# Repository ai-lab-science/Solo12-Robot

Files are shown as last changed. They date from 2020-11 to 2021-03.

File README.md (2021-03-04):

<!--
*** Thanks for checking out this README Template. If you have a suggestion that would
*** make this better, please fork the repo and create a pull request or simply open
*** an issue with the tag "enhancement".
*** Thanks again! Now go create something AMAZING! :D
***
***
***
*** To avoid retyping too much info. Do a search and replace for the following:
***  PRGeeesus, Solo12-Robot, twitter_handle, email
-->

<!-- PROJECT SHIELDS -->
<!--
*** I'm using markdown "reference style" links for readability.
*** Reference links are enclosed in brackets [ ] instead of parentheses ( ).
*** See the bottom of this document for the declaration of the reference variables
*** for contributors-url, forks-url, etc. This is an optional, concise syntax you may use.
*** https://www.markdownguide.org/basic-syntax/#reference-style-links
-->
<!--
[![Contributors][contributors-shield]][contributors-url]
[![Forks][forks-shield]][forks-url]
[![Stargazers][stars-shield]][stars-url]
[![Issues][issues-shield]][issues-url]
[![MIT License][license-shield]][license-url]
[![LinkedIn][linkedin-shield]][linkedin-url]

-->

<!-- PROJECT LOGO -->
<br />
<p align="center">
  
  <h3 align="center">Solo12-Robot</h3>

  <p align="center">
    This repo summarizes my changes to the Open Dynamics Robot Initiative Project.
    <br />
    <a href="https://github.com/ai-lab-science/Solo12-Robot"><strong>Explore the docs »</strong></a>
    <br />
    <br />
    <a href="https://github.com/ai-lab-science/Solo12-Robot">View Demo</a>
    ·
    <a href="https://github.com/ai-lab-science/Solo12-Robot/issues">Report Bug</a>
    ·
    <a href="https://github.com/ai-lab-science/Solo12-Robot">Request Feature</a>
  </p>
</p>

<!-- TABLE OF CONTENTS -->
## Table of Contents

* [About the Project](#about-the-project)
  * [Useful Links](#Useful-Links)
* [Changes Made to Original](#All-changes-Made-to-Original)
  * [Magnetic Encoder](#Magnetic-Encoder)
  * [M3 Belts and Pulleys](#M3-Belts-and-Pulleys)
  * [Motor and Center Pulley](#Motor-and-Center-Pulley)
  * [20x20 Hip AA Bearings](#20x20-Hip-AA-Bearings)
  * [Foot Contact Switch](#Foot-Contact-Switch)

* [Supplier Links](#Supplier-Links)
* [License](#license)
* [Contact](#contact)
* [Acknowledgements](#acknowledgements)

<!-- ABOUT THE PROJECT -->
## About The Project
TODO
TODO

#### Useful Links

* [Original Project by the Open Dynamic Robot Initiative](https://github.com/open-dynamic-robot-initiative/open_robot_actuator_hardware)

* [To-Dos for this Project](https://github.com/ai-lab-science/Solo12-Robot/issues)

---
<!-- All changes Made to Original -->
## All changes made to the original

Here you can find the Documentation of all changes that were made to the original Robot.

---
### Magnetic Encoder

The original Robot uses an optical Encoder. Due to its cost and the effort in assembly this was replaced with a magbetic enoder by AMS called [AS5047](https://ams.com/AS5047P).

| Encoder Changes Mechanical | Encoder Changes Electrical | Config. and Arduino | uDriver |
|---|---|---|---|
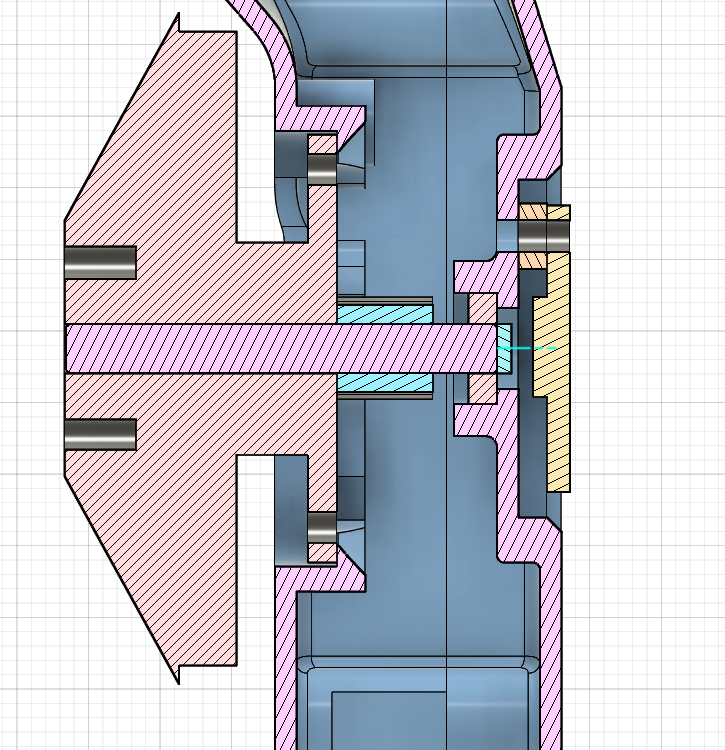
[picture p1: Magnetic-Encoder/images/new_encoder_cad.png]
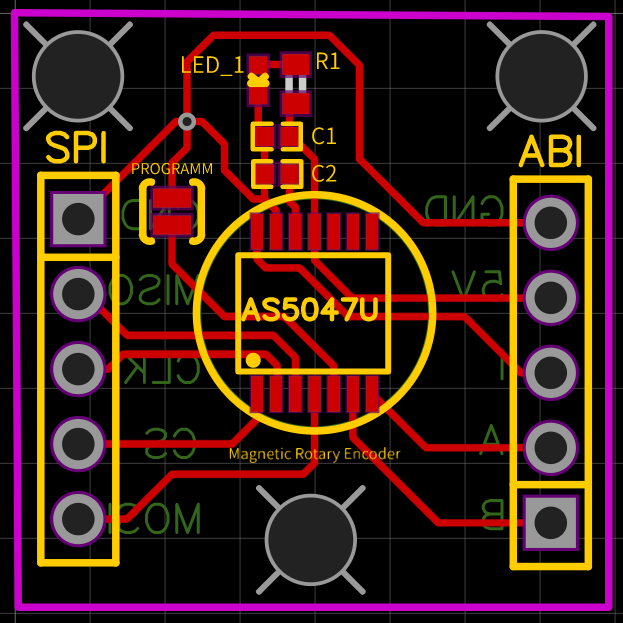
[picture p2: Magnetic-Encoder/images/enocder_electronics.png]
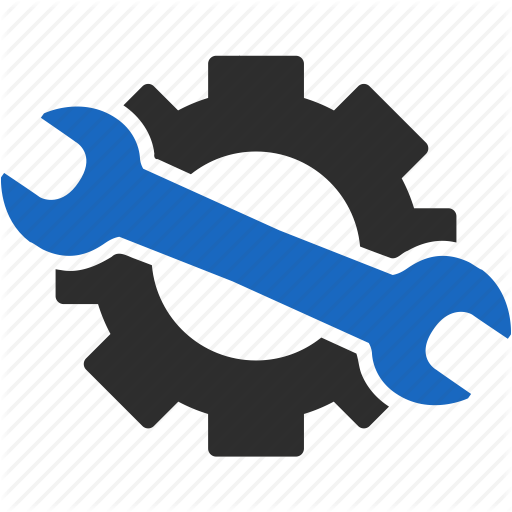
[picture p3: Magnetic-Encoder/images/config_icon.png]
| |  | ||

<!-- M3 Belts and Pulleys -->
---
### M3 Belts and Pulleys
The original Pulleys and Belts were repalced with M3 Pulleys and the fitting Belts.

* The new Belts were bought [here](https://www.zahnriemen24.de/a/40007-zahnriemen-3m)
* The new Pulleys were bought [here](https://www.zahnriemen24.de/a/40139-zahnscheiben-3m?vorbohrungspannsatz=1&bohrung=1&zaehnezahl=10&quantity=1)

The .STL files of the Pulleys were also updated:
|center pulley|Output Pulley|
|---|---|
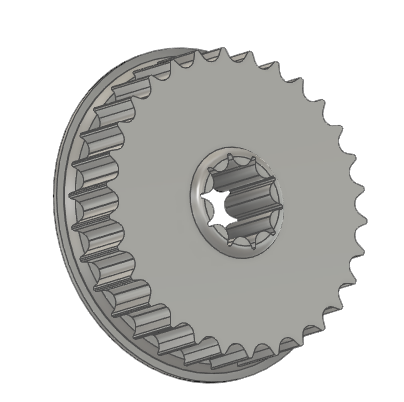
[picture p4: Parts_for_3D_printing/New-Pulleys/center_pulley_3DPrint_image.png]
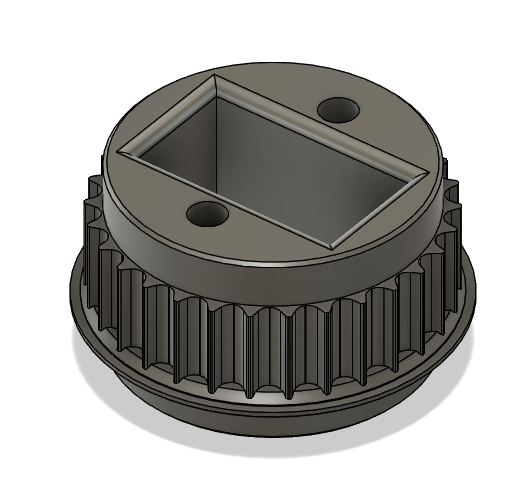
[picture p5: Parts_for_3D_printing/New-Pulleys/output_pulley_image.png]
|||
|[.stl New Center Pulley](Parts_for_3D_printing/New-Pulleys/pulley_center_30t.stl)|[.stl New Output Pulley](Parts_for_3D_printing/New-Pulleys/pulley_output_30t.stl)|

---
### Motor and Center Pulley
The Motor Pulley, Center Pulley and Motor Shaft were machined according to:
| |Motor Pulley|Center Pulley|Motor Shaft|
|---|---|---|---|
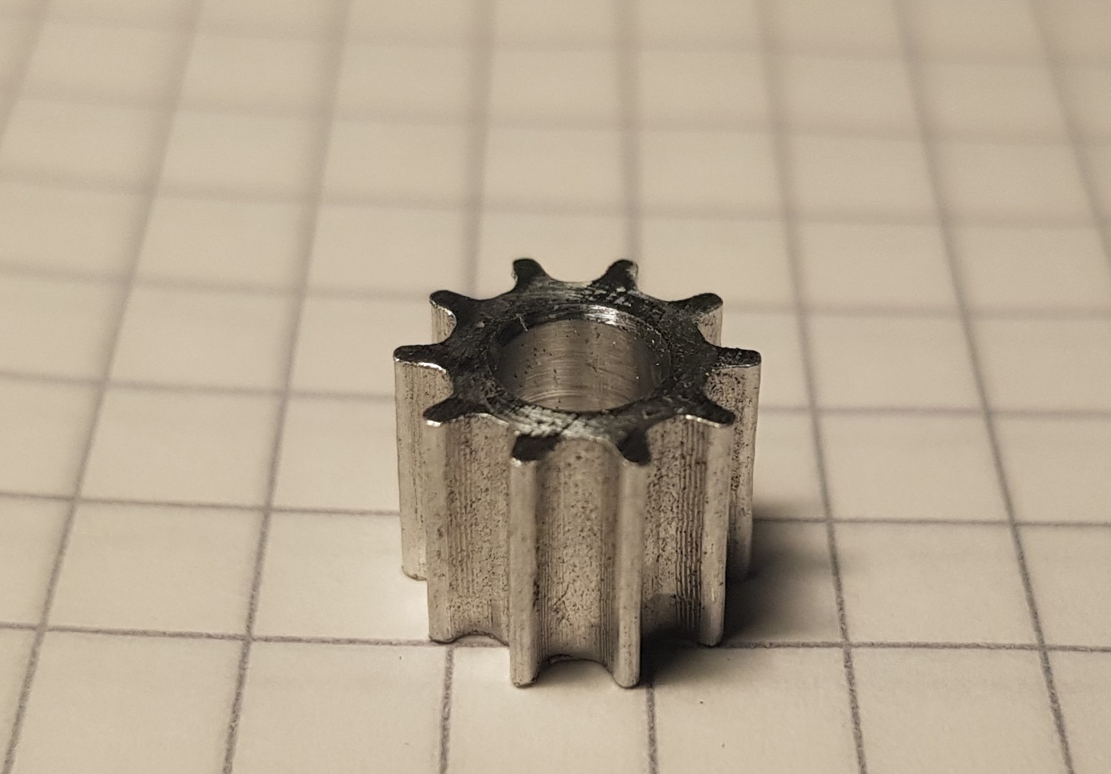
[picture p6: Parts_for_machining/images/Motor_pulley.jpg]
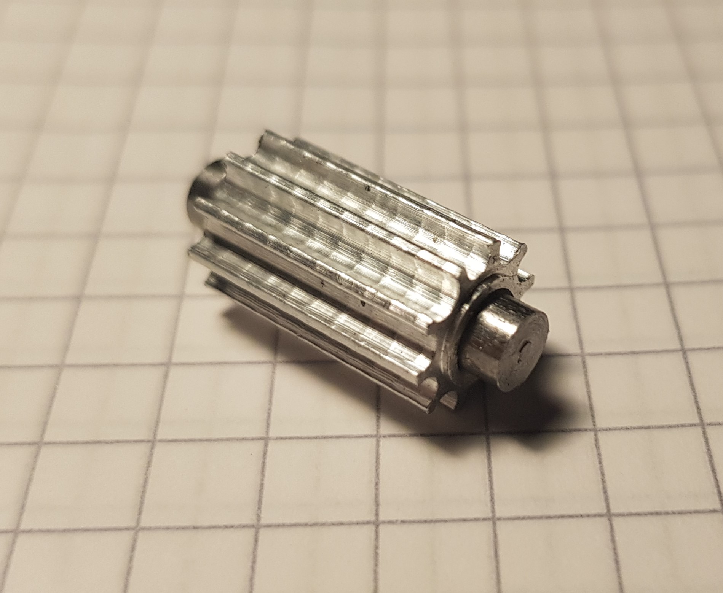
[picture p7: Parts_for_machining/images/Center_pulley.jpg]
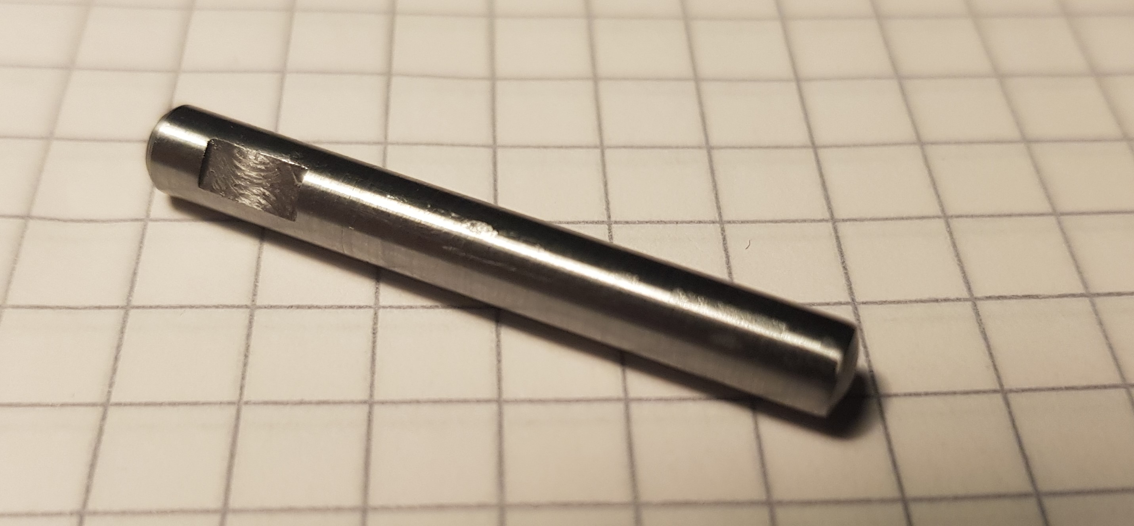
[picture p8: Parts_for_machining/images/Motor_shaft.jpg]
|Manufactured:||||
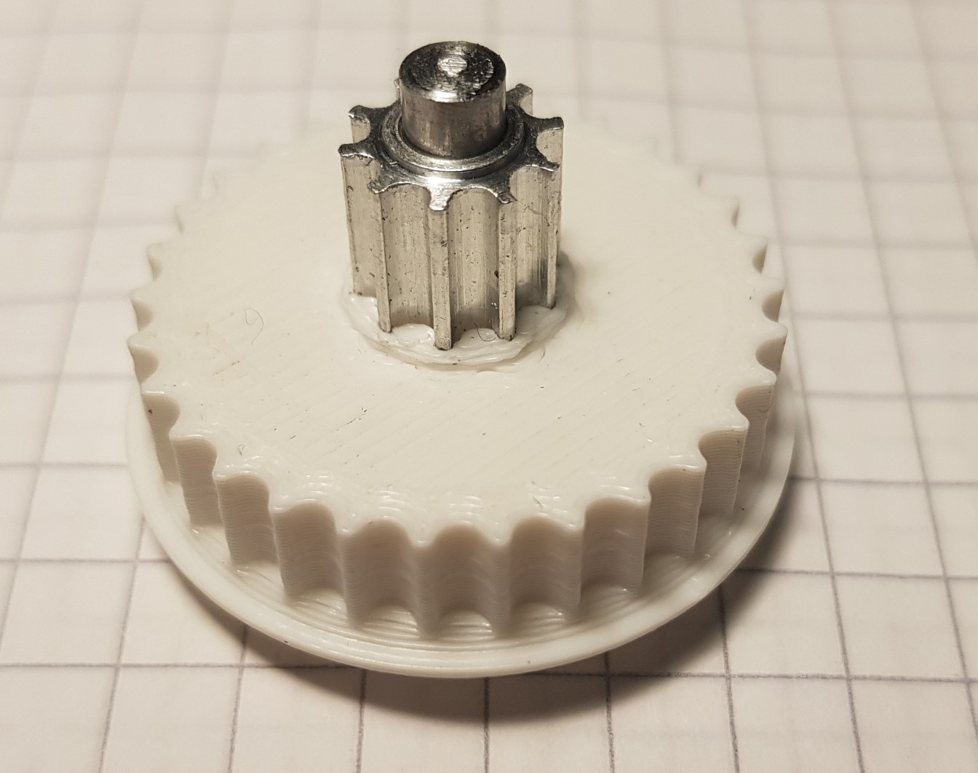
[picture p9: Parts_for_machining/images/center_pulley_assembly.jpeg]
|Assembly||||
|Machining Instructions PDF:|<a href="\Parts_for_machining\new_motor_Pulley_Zeichnung_v2.pdf" target="_blank">Motor Pulley</a>|<a href="\Parts_for_machining\New_Center_Pulley_10_teeth_Zeichnung_v0.pdf" target="_blank">Center Pulley</a>|<a href="\Parts_for_machining\motor_antigravity_4004_custom_shaft_Zeichnung_v1.pdf" target="_blank">Motor shaft</a>

* Parts in a lathe until they matched the Drawings:

<br>
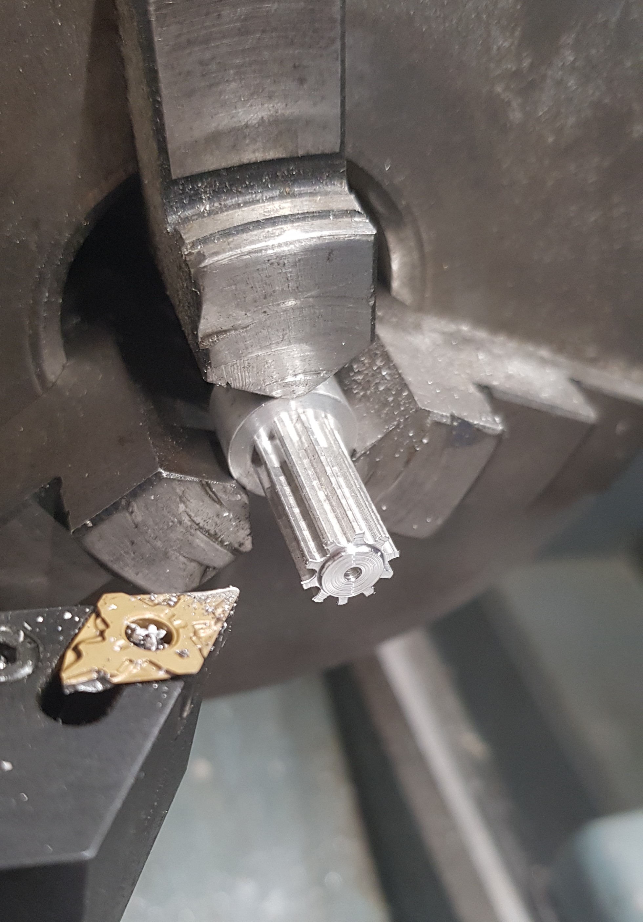
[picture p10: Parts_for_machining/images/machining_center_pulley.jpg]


---
### 20x20 Hip AA Bearings
 The "Hip AA Bearing" of size 25 x 20 x 4mm were replaced with bearings of 27 x 20 x 4mm because of availability. The [.stl](\Parts_for_3D_printing\hip_aa_fromt_cover_27.2mm_bearing.stl) files were updated accordingly. The bearings were bought [here](https://www.123kugellager.de/lager-R2520-2Z-ZEN).

---
### Foot Contact Switch

* no foot contact switch was added yet. However, the cables are fed through for future add-on.
[Link](Foot-Contact-Switch/README.md)

## Supplier Links
All other parts were bought as described. I divided the Project into 3 parts.
Here is a table for all parts from the Main Body:

| Part | Description | Suppliers |
|---|---|---|
| Hip AA Bearing | Bearing to attach Hip FE to the body | [123kugellager.de](https://store-en.tmotor.com/goods.php?id=438)|
| Fasteners | All fasteners as described by the original  | [online-schrauben.de](https://online-schrauben.de/shop/) |
<br>
Here is a table for all parts for one 3 DoF Leg:<br><br>

| Part | Description | Suppliers |
|---|---|---|
| T-Motor Antigravity 4004 300kV | Motor for the actuator | [T-Motor Store](https://www.123kugellager.de/lager-R2520-2Z-ZEN)|
| Fasteners | All fasteners as described by the original  | [online-schrauben.de](https://online-schrauben.de/shop/) |
| Timing Belt 4mm / length: 150mm / 50 teeth | new M3 Timing Belts  | [www.zahnriemen24.de](https://www.zahnriemen24.de/a/40007-zahnriemen-3m) |
| Timing Belt 6mm / length: 201mm / 67 teeth | new M3 Timing Belts  | [www.zahnriemen24.de](https://www.zahnriemen24.de/a/40007-zahnriemen-3m) |
|Bearing Output Shaft 32mm x 25mm x 4mm | bearing for each output | [ekugellager.de](https://www.ekugellager.de)|
|Bearing Motor Shaft and Center Shaft |8mm x 4mm x 2mm bearing | " |[ekugellager.de](https://www.ekugellager.de)|
|Bearing Timing Belt Tensioner| - | " |
|Motor Shaft| new shaft | [reidl.de](https://www.reidl.de/iso-8740-zylinderkerbstifte-mit-fase?q=stahlzylinder)
|Motor and Center Pulley| new M3 Pulleys| [www.zahnriemen24.de](https://www.zahnriemen24.de/a/40139-zahnscheiben-3m?vorbohrungspannsatz=1&bohrung=1&zaehnezahl=10&quantity=1)|

## License

Distributed under the MIT License. See `LICENSE` for more information.

<!-- CONTACT -->
## Contact

martin.buchschuster@student.uni-luebeck.de

Project Link: [This-site](https://github.com/ai-lab-science/Solo12-Robot)

<!-- ACKNOWLEDGEMENTS -->
## Acknowledgements

* [Ralf Bruder]()
* [Elmar Rueckert]()
* [Martin Buchschuster]()

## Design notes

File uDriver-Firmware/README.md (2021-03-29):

### Motorware modifications

The firmware of the uDrivers has to be modified:

* In the file "user_j1.h", "user_j5.h", "user_mtr_on_j1.h", "user_mtr_on_j5.h" #define USER_MOTOR_ENCODER_LINES changed to ().

| in file | output in SPI |
|---|---|
|133.7|852143|
|1024.0|65735|
|32768.0|28|
|65536.0|7|
|131072.0|3|
|262144.0|1|

---

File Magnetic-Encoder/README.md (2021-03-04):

## Encoder Adaptation

The Optical encoder, enocder wheel and mount were replaces woth a magentic encoder.
For this, the AS5047 is mounted facing the end of the of shaft, to which a magnet is attached.
The Covers were modified to accept the footprint of the PCB.
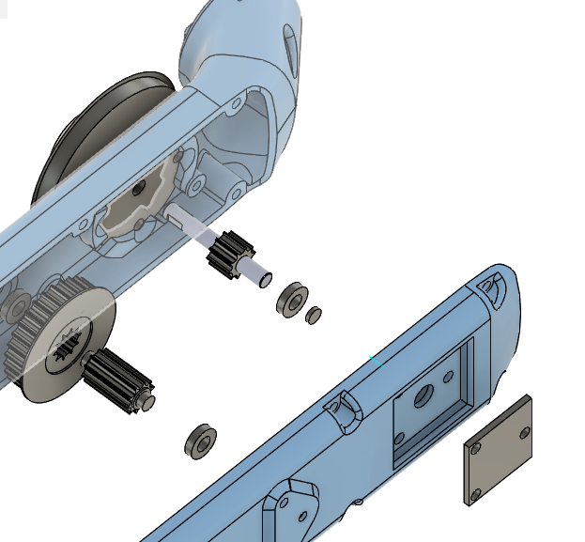
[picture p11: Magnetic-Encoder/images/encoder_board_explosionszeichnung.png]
<br><br>

## Mechanical Changes

All the covers of the leg modules were equipped with a recess of 3mm debth to hold the encoder board. The Motor-shaft was shortened by 3mm aswell. At the end of the shaft now sits a magnet that gives the rotational inofrmation to the AS5074.
Three holes for mounting as well as spacers are also given.

---
### Magnet for the Encoder
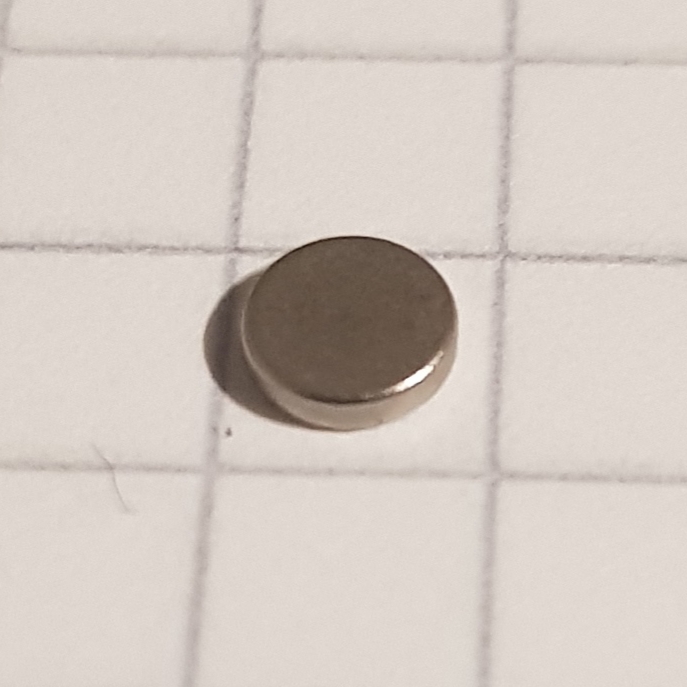
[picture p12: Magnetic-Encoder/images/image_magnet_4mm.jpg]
<br>
* [Magnets Retailer](https://www.magnetkontor.de/products/de/Neodym-Magnete-Rohmagnete/Auswahl-besond-Eigenschaft/diametral-magnetisiert/NdFeB-N52-Scheibenmagnet-4-x-1-mm-vernick-diametr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)<br>

---
### New Shell Covers

* The list of STL files for 3d printing the new shells can be found here: [STL files 3dof leg](stl_files). TODO: Link to new .stl Files

|Hip AA| Hip FE| Upper Leg|
|---|---|---|
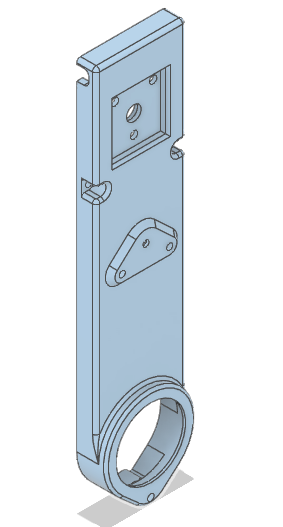
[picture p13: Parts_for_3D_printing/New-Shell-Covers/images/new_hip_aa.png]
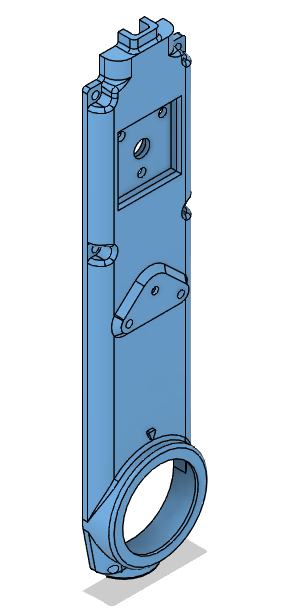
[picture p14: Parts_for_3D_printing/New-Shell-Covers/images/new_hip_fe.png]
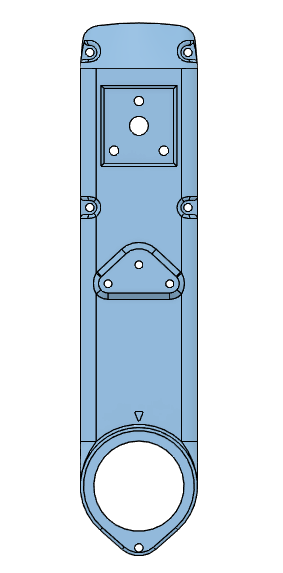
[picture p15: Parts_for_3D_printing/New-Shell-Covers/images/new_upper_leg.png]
|||
|[Hip AA Module New Shell Cover - STL file](../Parts_for_3D_printing/New-Shell-Covers/cover_hip_aa.STL)|[Hip FE Module New Shell Cover - STL file](../Parts_for_3D_printing/New-Shell-Covers/cover_hip_fe.STL)|[Upper Leg Module New Shell Cover - STL file](../Parts_for_3D_printing/New-Shell-Covers/cover_upper_leg.STL)

---
## Electrical changes

As the micro Drivers Require ABI input for the tourque control, the encoders can output ABI, as well as SPI in order tp have the position input ready for the [Master-Board](https://github.com/open-dynamic-robot-initiative/master-board#master-board).

---
### Gerber Files

|PCB Schematic|Photograph|
|---|---|
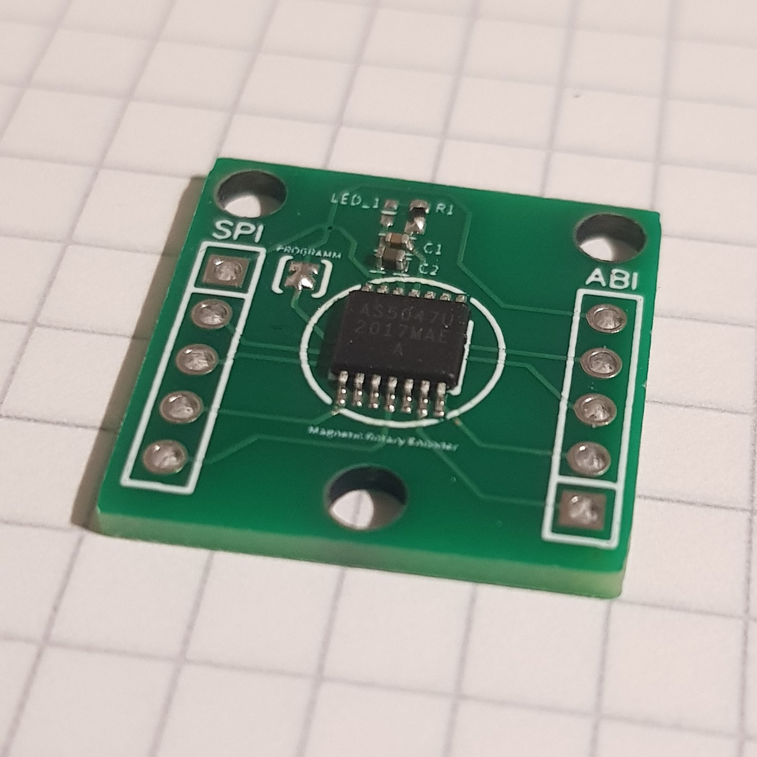
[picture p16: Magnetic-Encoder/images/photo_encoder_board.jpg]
|  | |

* The gerber files for the encoder Bord can be found [Here](/Electrical-Changes)

---
### Bill of Material

| Part | Description | Suppliers |
|---|---|---|
| AS5047 | main IC | [Mouser](mouser.com)|
| C1 | Cap. 0402 100 nf  | " |
| C2 | Cap. 0402 1 uf  | " |
| R1 | optional. 100R for LED_1  | " |
| LED_1 | 0402 LED  | " |

---
### Wires

* The magnetic encoders are wired with as two flatband cables. The colors are the same on all encoders.

|Flatband Cables|Description
|---|---|
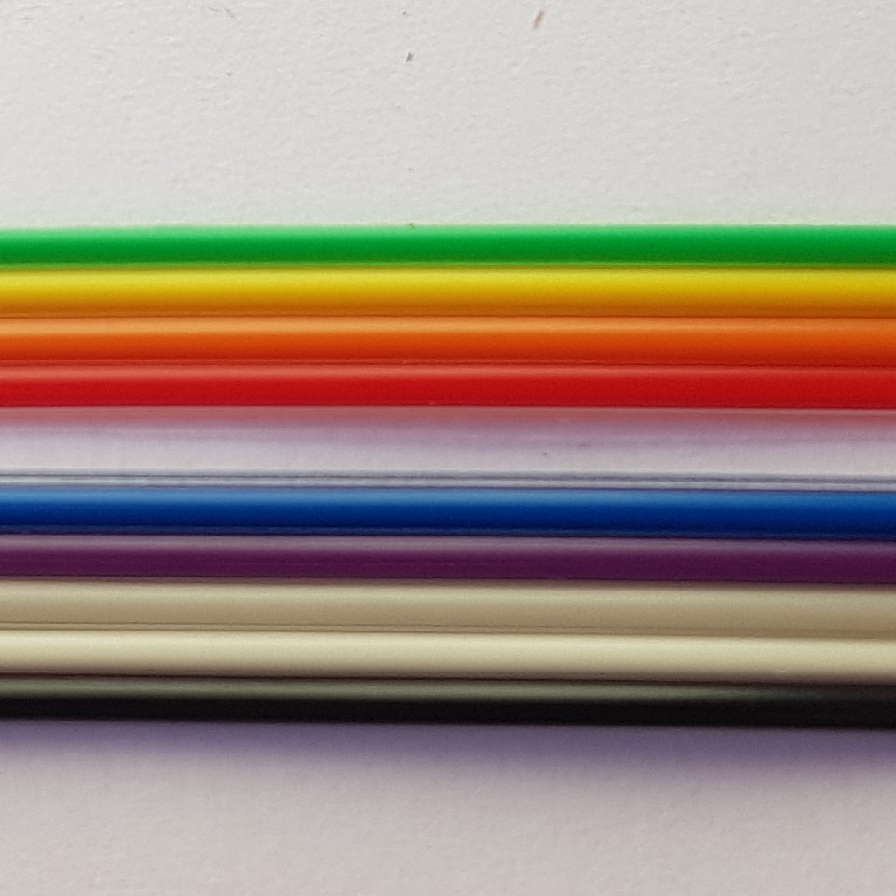
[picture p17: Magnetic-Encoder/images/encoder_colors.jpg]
|  |<table><thead><tr><th>Color</th><th>Pin</th> <th>Description</th></tr></thead><tbody><tr><td>Green</td><td>MOSI</td><td>Master Out Slave In (SPI)</td></tr><tr><td>Yellow</td><td>CS</td><td>chip Select (SPI)</td></tr><tr><td>Orange</td><td>CLK</td><td>clock (SPI)</td></tr><tr><td>Red</td><td>MISO</td><td>Master in Slave Out (SPI)</td></tr>
<tr><td>Marine Blue</td><td>B</td><td>for ABI</td></tr><tr><td>Purple</td><td>A</td><td>"</td></tr><tr><td>Grey</td><td>I</td><td>"</td></tr><tr><td>White</td><td>5V</td><td>Power supply</td></tr><tr><td>Black</td><td>GND</td><td>Ground for SPI and ABI</td></tr></tbody></table>|

<br>

---
## Communication Via Arduino

The AS5047 is should be connected via SPI [Wires](#Wires) to any other Arduino with SPI.
Then following Code can be used to program the AS5047 tempoararily. The solder bridge "Test" should be closed for this.
* [Code: Program AS5047U_OTP](Arduino)

By removing the while(1) the programming will be OTP.

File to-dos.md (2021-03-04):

# TODOS for this Project:

|Name|Descriptions|
|----|----|
|Foot contact Sensor|Add a foot contact sensor to all legs. The cables are already existing. The ODRI also had a Sensor designed already|
|Order Extra Cables|Some cabls to connect all the sencors to the uDrivers Are still missing. <br>[Details Electronic Components and Tools](https://github.com/open-dynamic-robot-initiative/open_robot_actuator_hardware/blob/master/electronics/details/details_components.md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)

<!--Test->

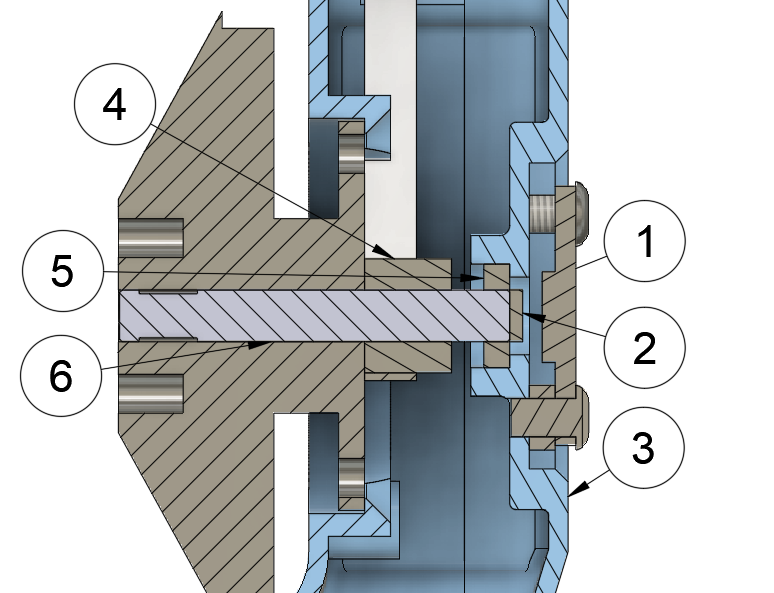
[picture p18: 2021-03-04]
Magnetic-Encoder/images/overview_2.png

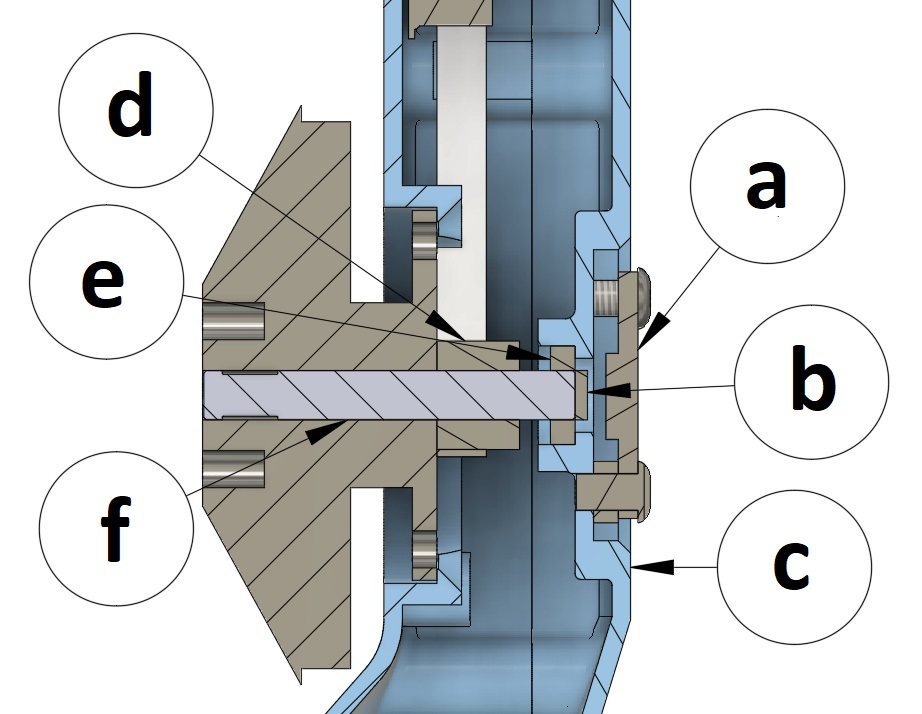
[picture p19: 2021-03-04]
Magnetic-Encoder/images/overview_1_letters.jpg

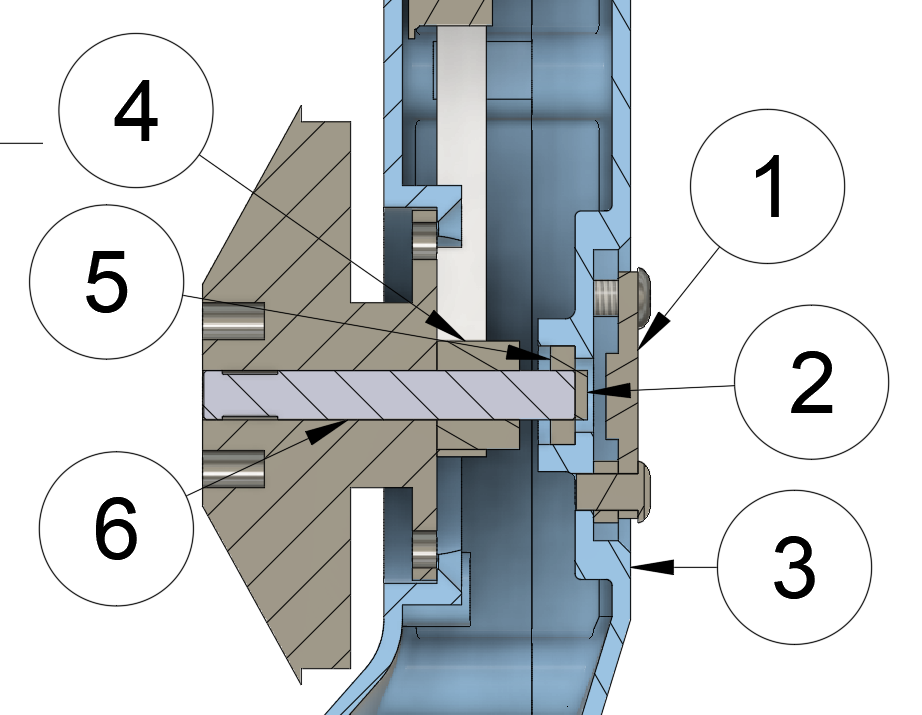
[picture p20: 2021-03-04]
Magnetic-Encoder/images/overview_1.png

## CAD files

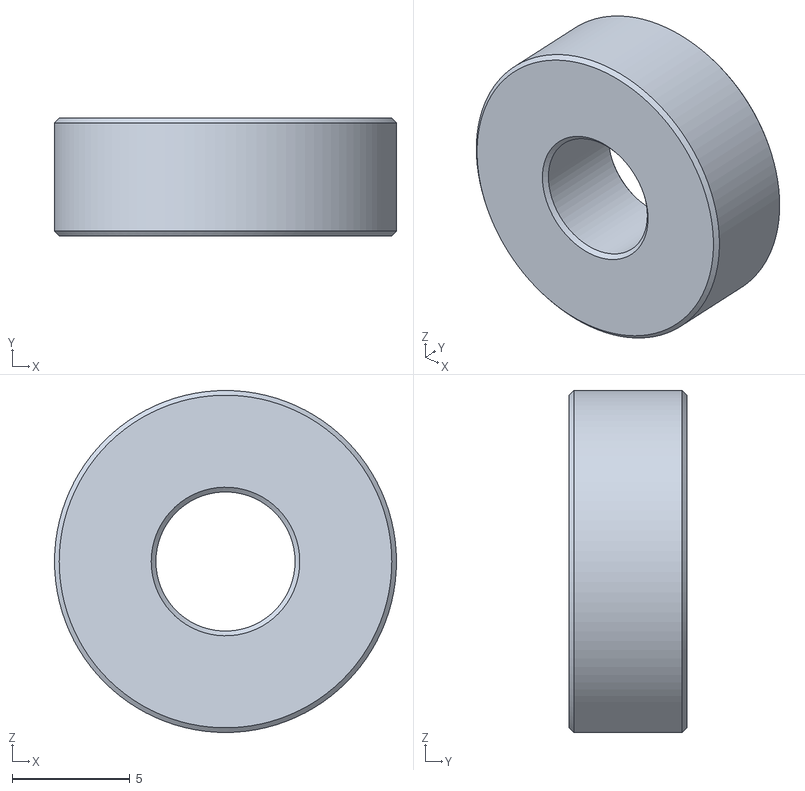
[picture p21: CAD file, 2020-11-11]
Parts_for_3D_printing/Werkzeuge/tool_center_pulley_assembly.stl
14.5 x 5.00 x 14.5

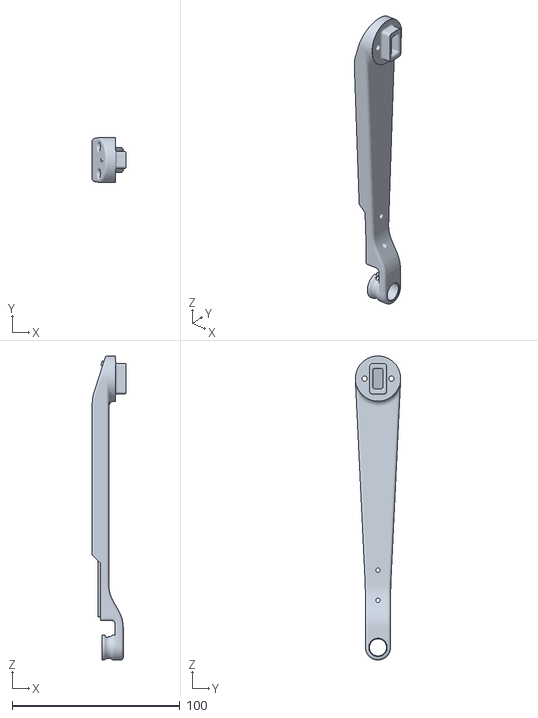
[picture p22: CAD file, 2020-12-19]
Parts_for_3D_printing/Foot/main Body.stl
20.0 x 27.0 x 181.0

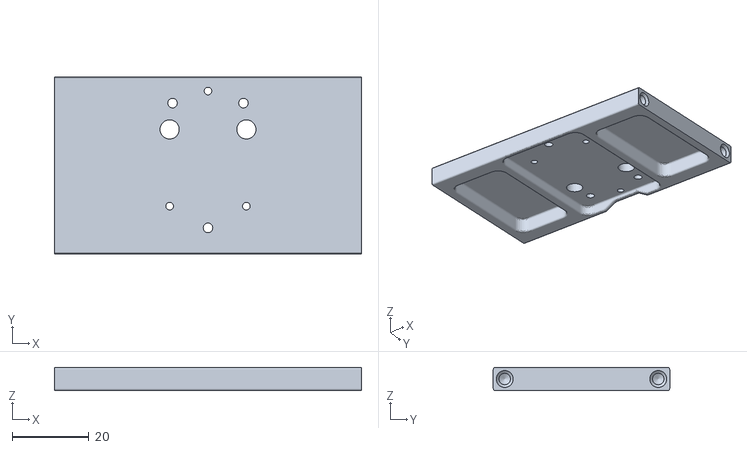
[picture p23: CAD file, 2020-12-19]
Parts_for_3D_printing/Body_new_IMU.stl
80.0 x 46.0 x 6.00

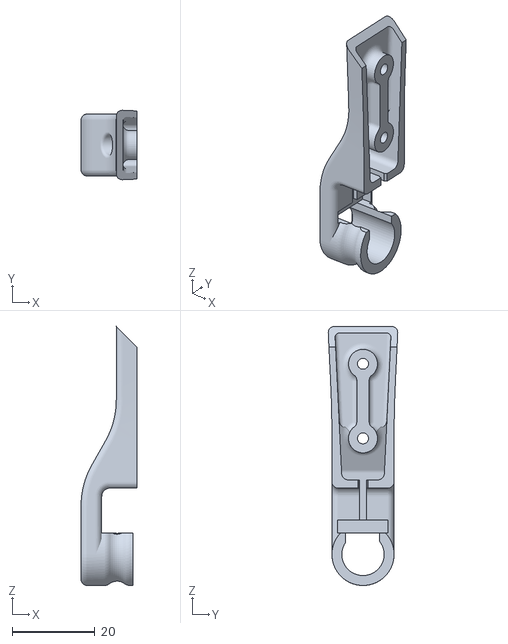
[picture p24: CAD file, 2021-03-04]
Parts_for_3D_printing/Foot/ankle_new_2.stl
13.5 x 16.8 x 62.5

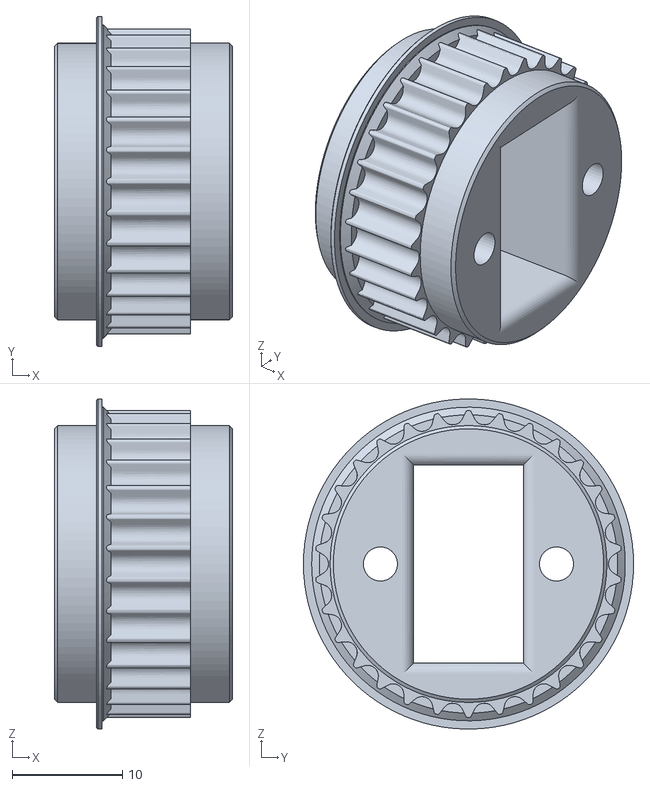
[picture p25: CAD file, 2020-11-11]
Parts_for_3D_printing/New-Pulleys/pulley_output_30t.stl
16.2 x 30.0 x 30.0

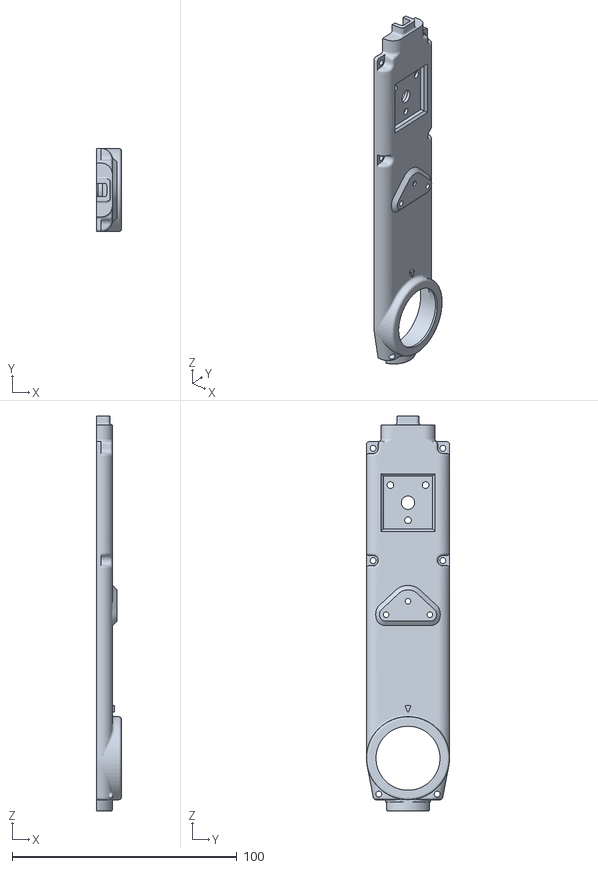
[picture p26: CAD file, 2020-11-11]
Parts_for_3D_printing/New-Shell-Covers/cover_hip_fe.stl
11.0 x 37.0 x 175.9

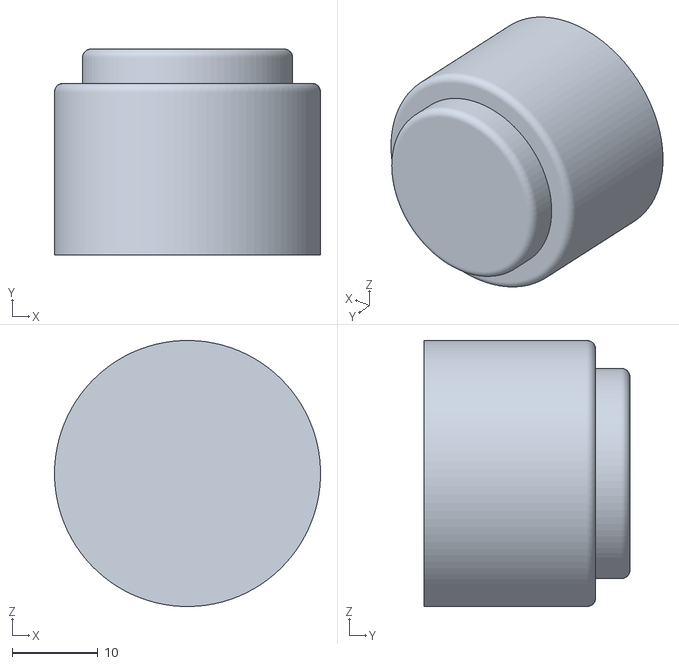
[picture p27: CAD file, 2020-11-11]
Parts_for_3D_printing/Werkzeuge/uotput_bearing_die.stl
31.0 x 24.0 x 31.0

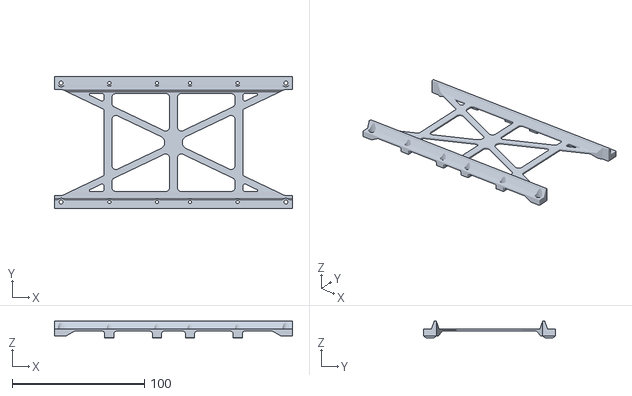
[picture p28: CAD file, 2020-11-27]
Parts_for_3D_printing/body_structure_center.STL
180.0 x 100.0 x 12.5

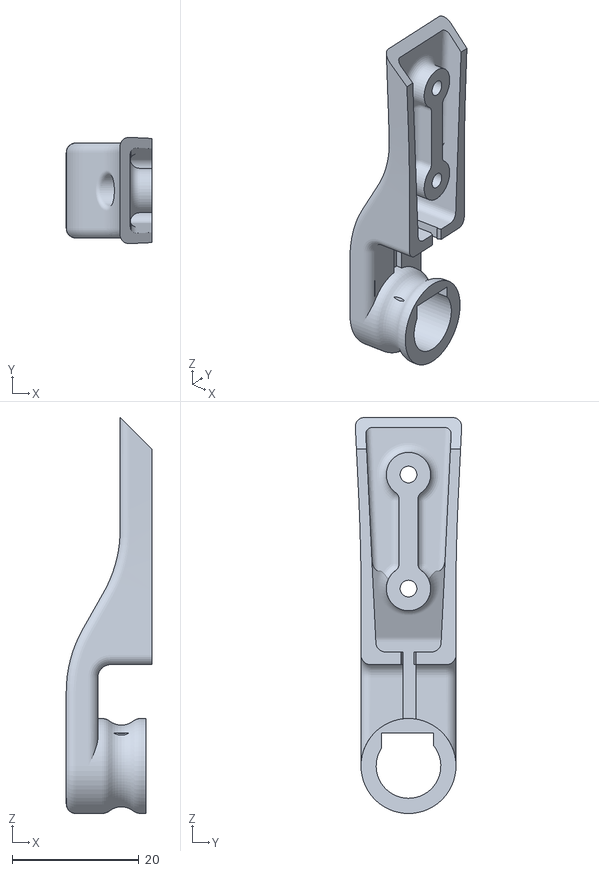
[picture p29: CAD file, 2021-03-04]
Parts_for_3D_printing/Foot/ankle_new_3.stl
13.5 x 16.8 x 62.5

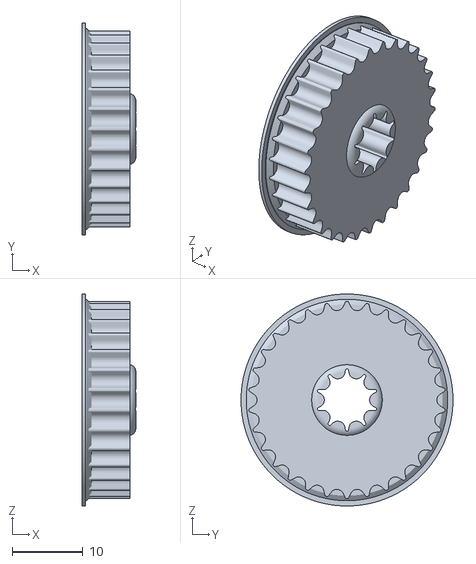
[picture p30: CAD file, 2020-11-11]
Parts_for_3D_printing/New-Pulleys/pulley_center_30t.stl
7.60 x 30.0 x 30.0

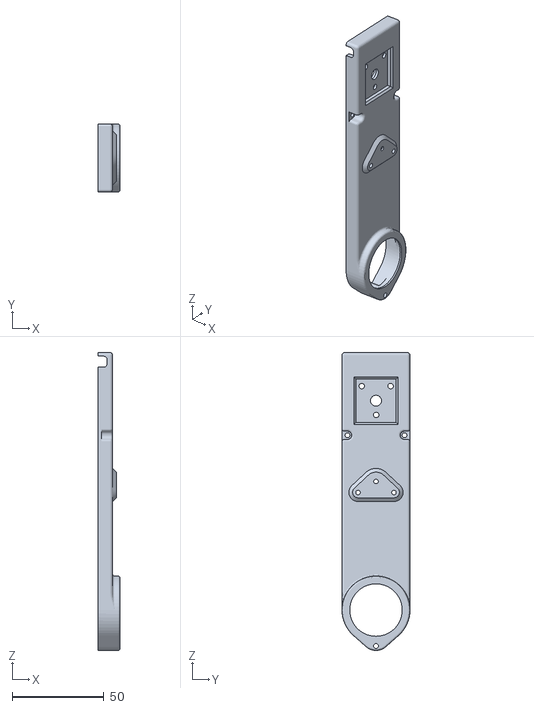
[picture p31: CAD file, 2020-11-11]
Parts_for_3D_printing/New-Shell-Covers/cover_hip_aa.stl
12.0 x 37.0 x 162.0

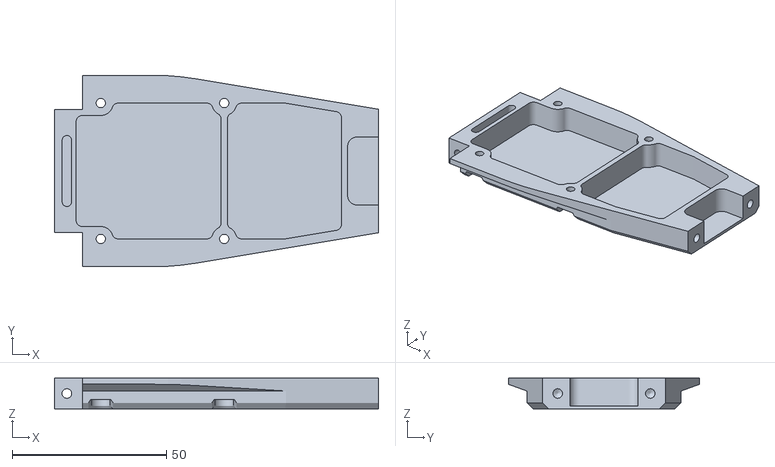
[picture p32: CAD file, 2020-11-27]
Parts_for_3D_printing/body_structure_side.STL
105.0 x 62.0 x 10.0

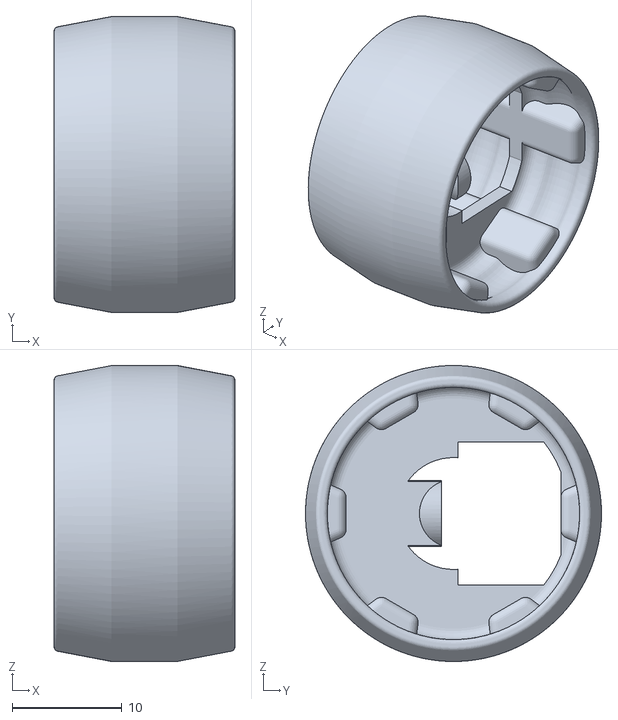
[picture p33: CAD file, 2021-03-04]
Parts_for_3D_printing/Foot/foot_palm_new_2.stl
16.5 x 27.0 x 27.0

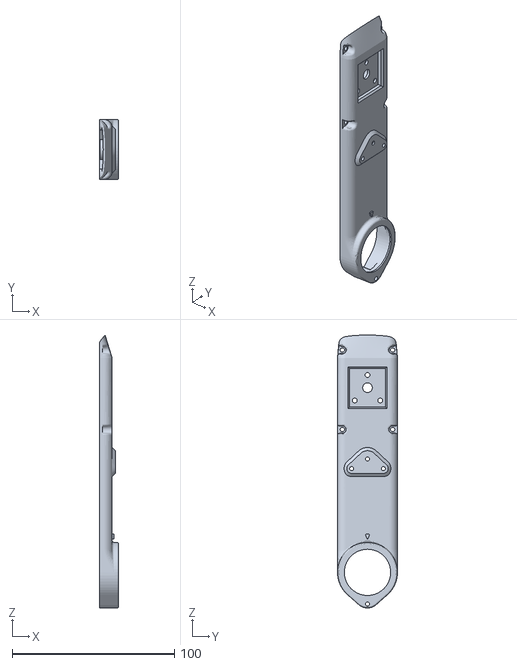
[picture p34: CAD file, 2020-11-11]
Parts_for_3D_printing/New-Shell-Covers/cover_upper_leg.stl
12.0 x 37.0 x 168.3

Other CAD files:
Parts_for_3D_printing/Werkzeuge/motor_shaft_extractor.stl
Parts_for_3D_printing/body_structure_center_handle.STL
Parts_for_3D_printing/Foot/foot_new_3.stl
Parts_for_3D_printing/Werkzeuge/center_pulley_protection v2.stl
Parts_for_3D_printing/AI3M_print2_file.3mf
Parts_for_3D_printing/Foot/Ankle.stl
Parts_for_3D_printing/Foot/Bootom of Foot.stl
Parts_for_3D_printing/Foot/Foot_new_2.stl
Parts_for_3D_printing/Foot/fake_platine.stl
Parts_for_3D_printing/Foot/foot_palm_new_3.stl
Parts_for_3D_printing/Martin_print2_side-fesupport_fecover.3mf
Parts_for_3D_printing/Martin_print3_3coveraa-1coverfe-1baseupperleg.3mf
Parts_for_3D_printing/Print_4.3mf
Parts_for_3D_printing/base_hip_aa.stl
Parts_for_3D_printing/base_hip_fe.stl
Parts_for_3D_printing/base_upper_leg.stl
Parts_for_3D_printing/body_structure_back.STL
Parts_for_3D_printing/body_structure_bottom.STL
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

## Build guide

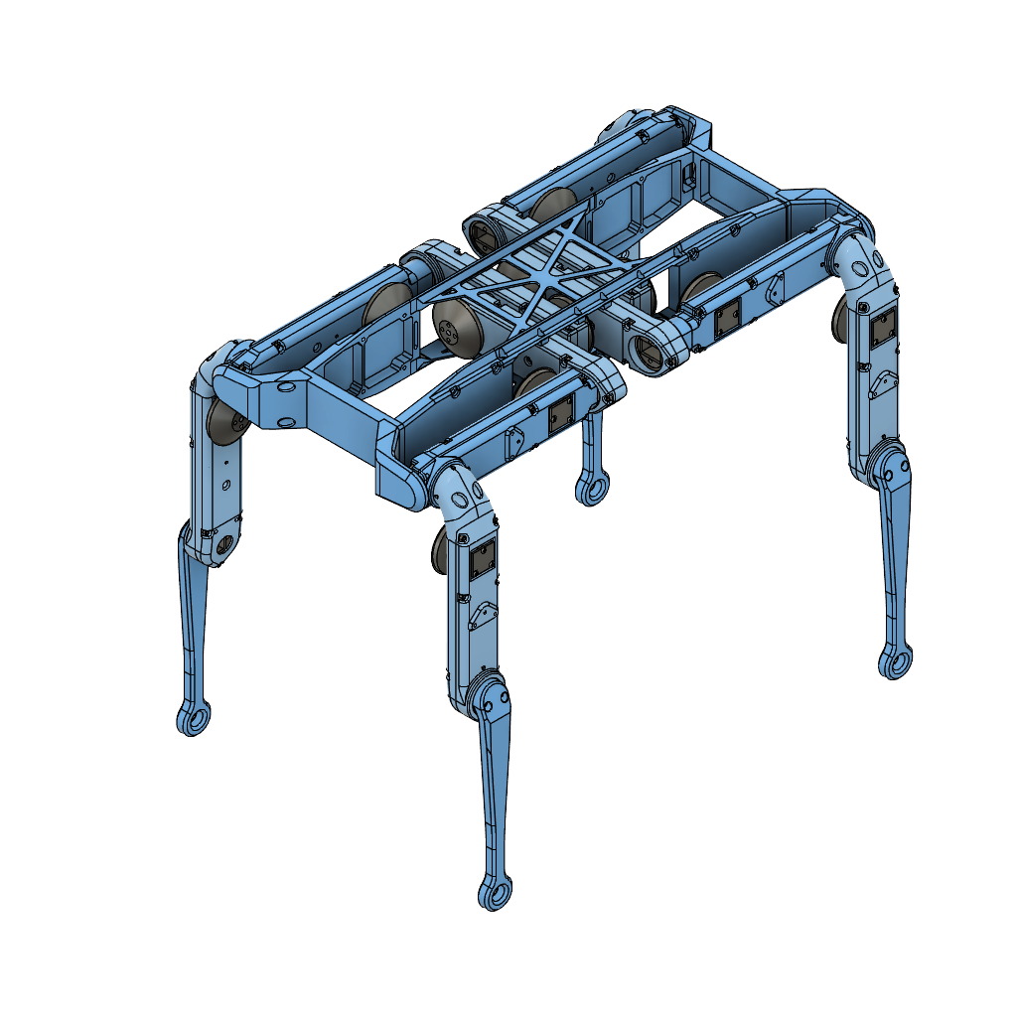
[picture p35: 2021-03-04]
images/Final Assembly v37.png

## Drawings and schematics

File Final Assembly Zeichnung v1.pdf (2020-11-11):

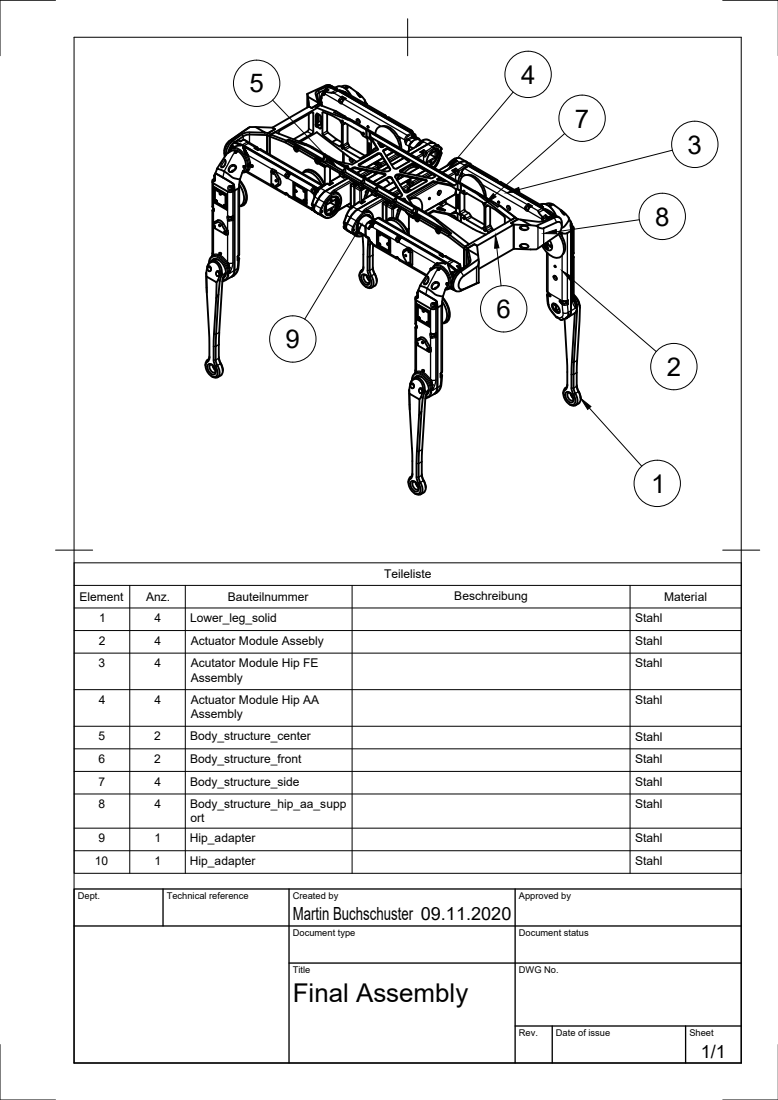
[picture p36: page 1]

Element | Anz. | Bauteilnummer | Beschreibung | Material

1 | 4 | Lower_leg_solid | | Stahl

2 | 4 | Actuator Module Assebly | | Stahl

3 | 4 | Acutator Module Hip FE Assembly | | Stahl

4 | 4 | Actuator Module Hip AA Assembly | | Stahl

5 | 2 | Body_structure_center | | Stahl

6 | 2 | Body_structure_front | | Stahl

7 | 4 | Body_structure_side | | Stahl

8 | 4 | Body_structure_hip_aa_supp ort | | Stahl

9 | 1 | Hip_adapter | | Stahl

10 | 1 | Hip_adapter | | Stahl

Dept. | Technical reference | Created by Martin Buchschuster 09.11.2020 | Approved by

Document type | Document status

Title Final Assembly | DWG No.

Rev. | Date of issue | Sheet 1/1

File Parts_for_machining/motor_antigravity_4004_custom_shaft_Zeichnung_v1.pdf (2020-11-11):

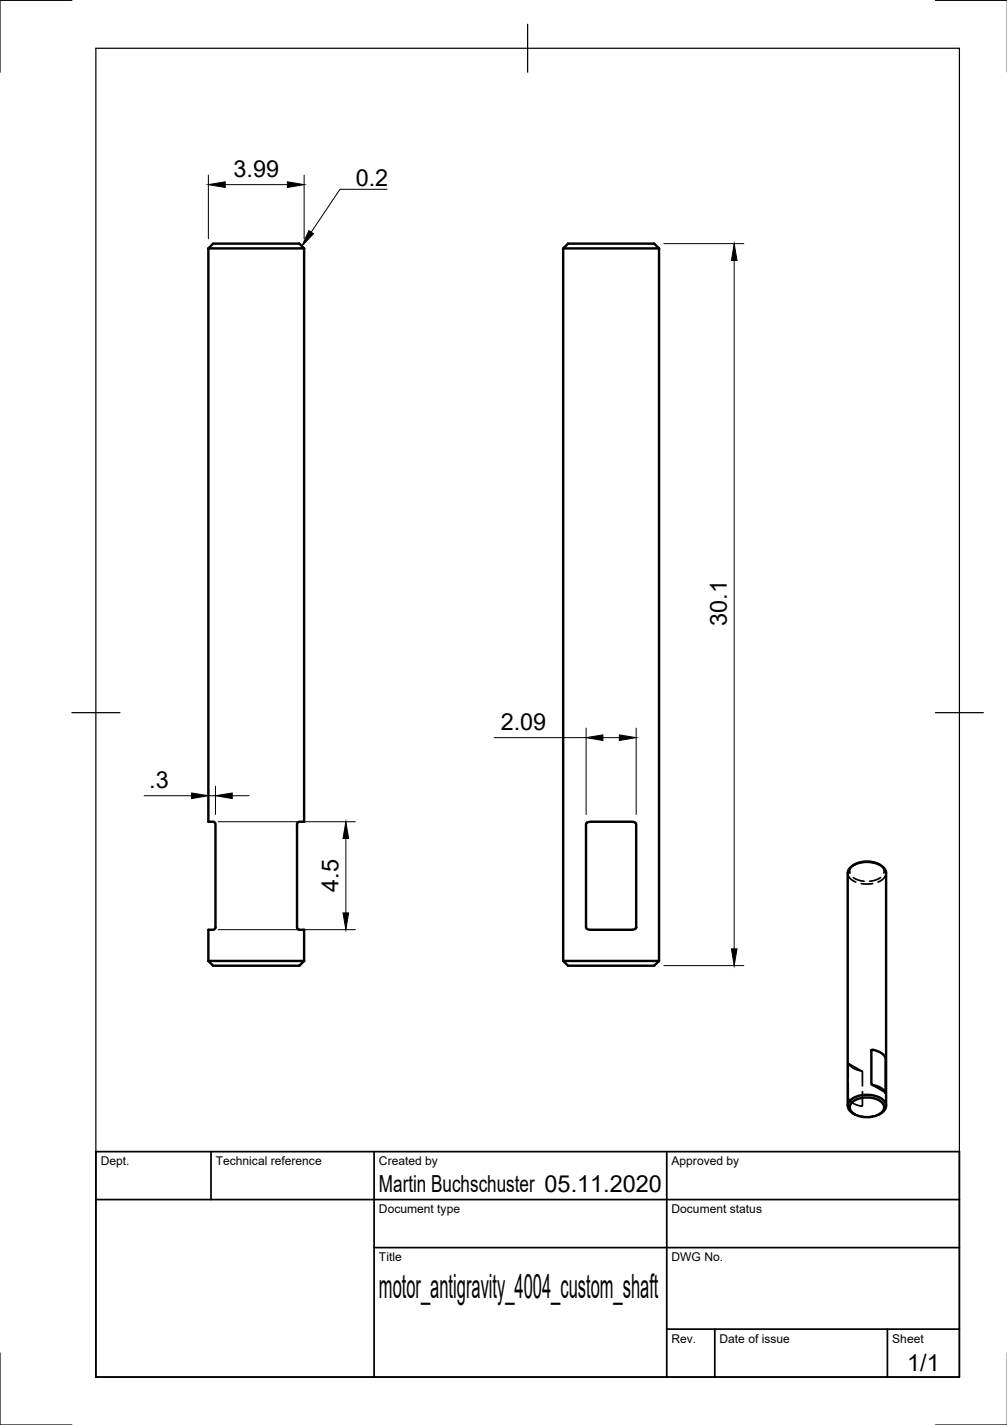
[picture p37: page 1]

Dept. | Technical reference | Created by Martin Buchschuster 05.11.2020 | Approved by

Document type | Document status

Title motor_antigravity_4004_custom_shaft | DWG No.

Rev. | Date of issue | Sheet 1/1

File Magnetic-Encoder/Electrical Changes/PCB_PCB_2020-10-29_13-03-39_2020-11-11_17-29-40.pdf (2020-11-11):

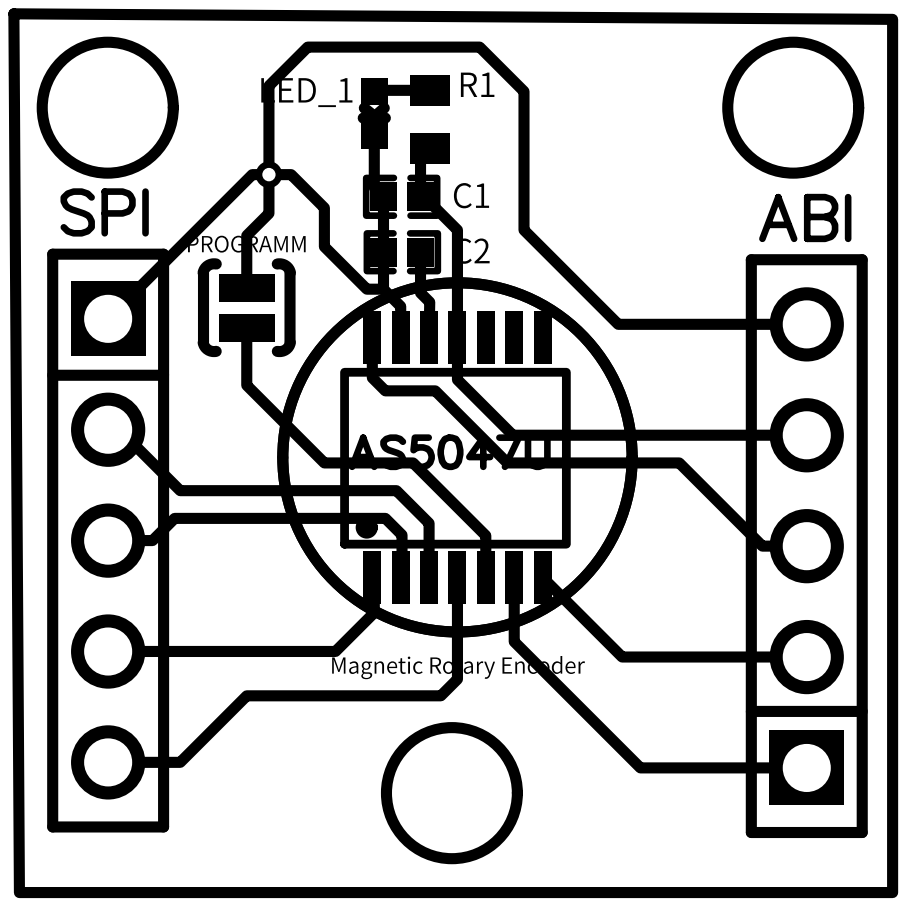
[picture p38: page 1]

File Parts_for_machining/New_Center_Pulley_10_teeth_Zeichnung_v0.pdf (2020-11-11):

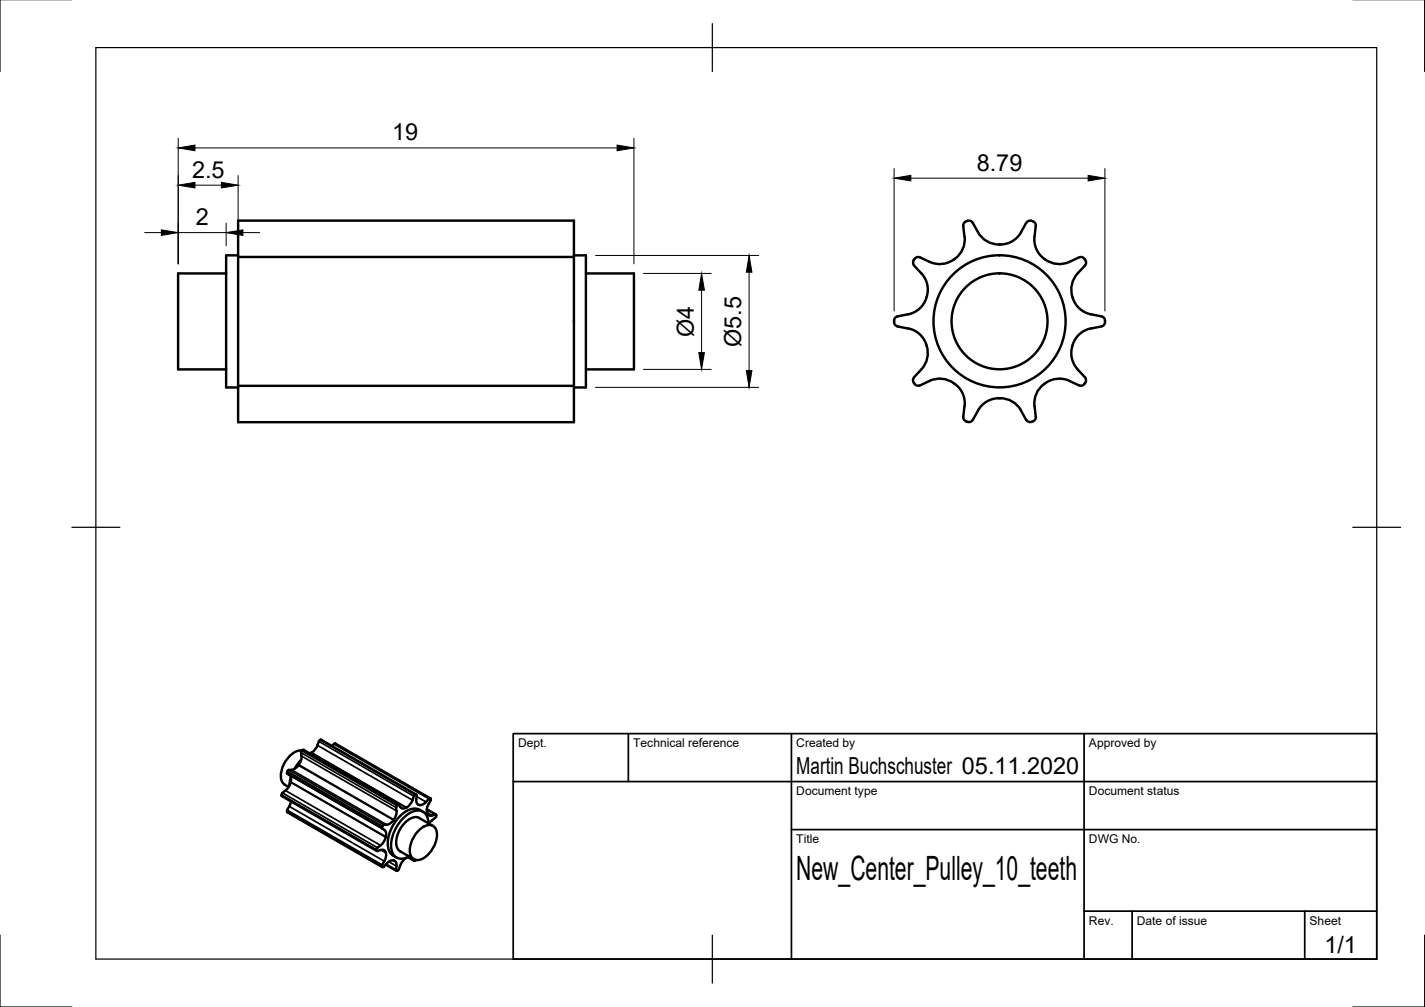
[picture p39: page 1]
Martin Buchschuster Ø4

Dept. | Technical reference | Created by 05.11.2020 | Approved by

Document type | Document status

Title New_Center_Pulley_10_teeth | DWG No.

Rev. | Date of issue | Sheet 1/1

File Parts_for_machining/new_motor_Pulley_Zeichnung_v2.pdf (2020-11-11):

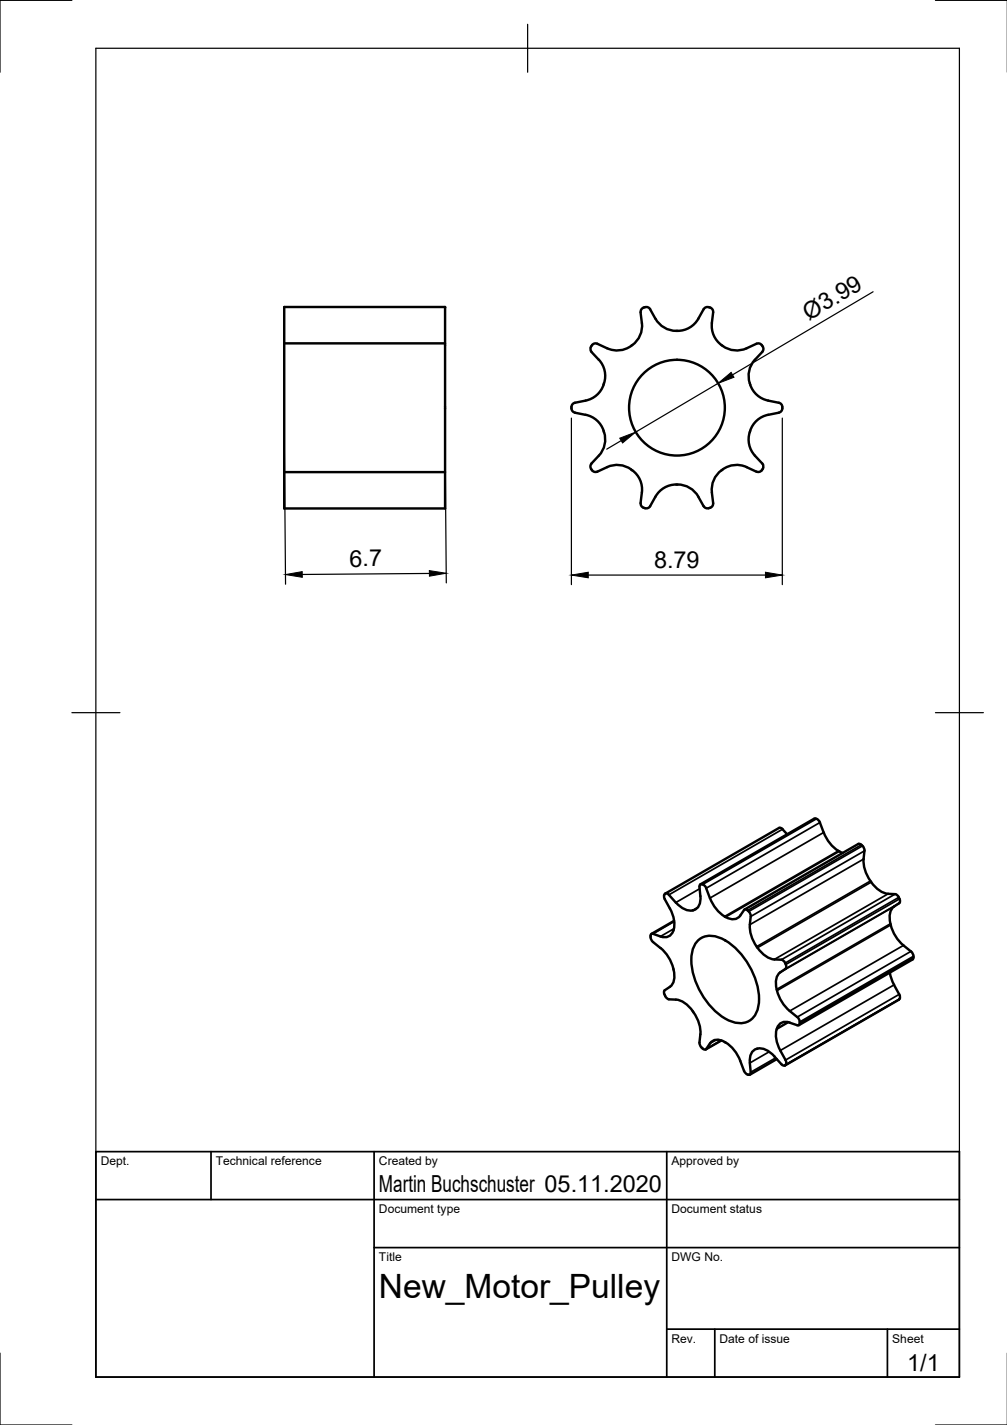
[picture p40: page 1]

Dept. | Technical reference | Created by Martin Buchschuster 05.11.2020 | Approved by

Document type | Document status

Title New_Motor_Pulley | DWG No.

Rev. | Date of issue | Sheet 1/1

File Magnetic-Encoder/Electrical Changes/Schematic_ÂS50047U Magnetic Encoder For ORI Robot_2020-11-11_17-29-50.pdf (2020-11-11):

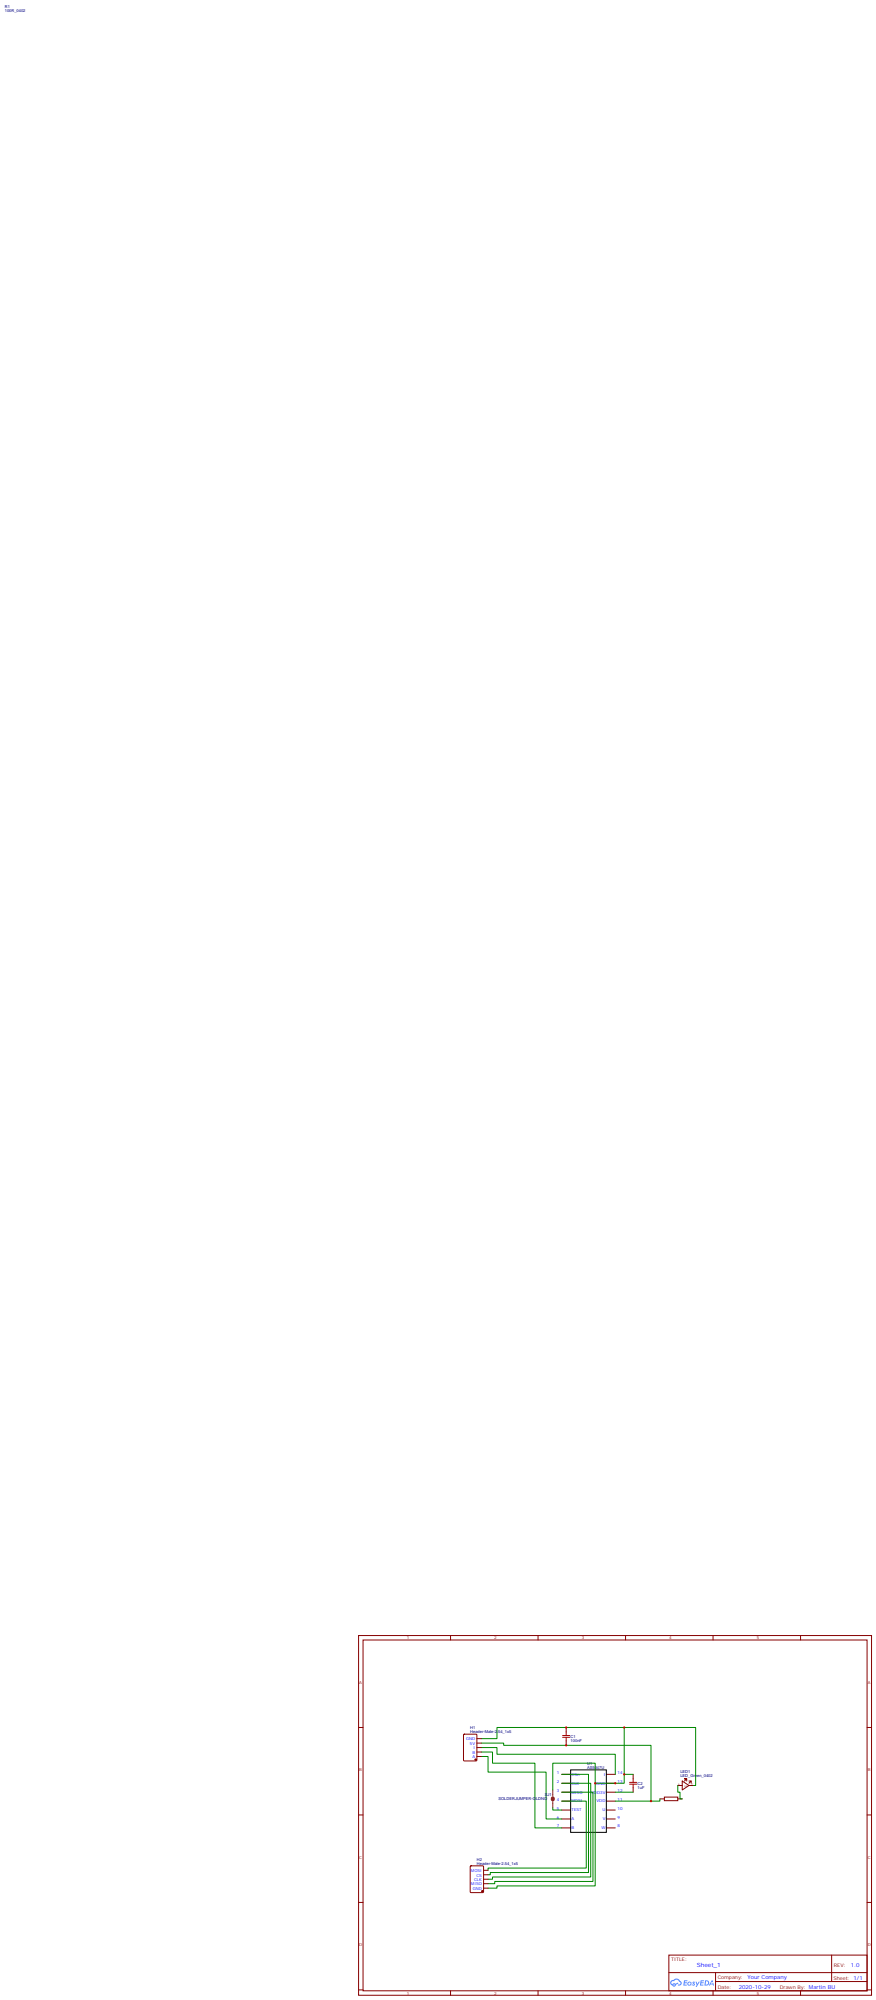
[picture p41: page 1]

Drawn By: Martin BU

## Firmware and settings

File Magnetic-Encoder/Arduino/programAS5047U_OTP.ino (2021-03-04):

#include <SPI.h>

// OTP non-volatile programming
// 1. Power on cycle
// 2. Write the SETTINGS1 and SETTINGS2 and SETTINGS3 registers with the Custom settings for this application
// 3. Place the magnet at the desired zero position
// 4. Read out the measured angle from the ANGLECOM register
// 5. Write ANGLECOM [5:0] into the ZPOSL register and ANGLECOM[13:6] into the ZPOSM register
// 6. Read reg(0x0016) to reg(0x001A)
// 7. Set ECC_en in Register ECC to 1 (ECC protection enabled)
// 8. Read ECC_s (0x3FD0) to get the correct ECC key
// 9. Write ECC_s key into ECC register
// 10. Read reg(0x0016) to reg(0x001B) → read register step1
// 11. Comparison of written content (settings and angle) with content of read register step1
// 12. If point 11 is correct, enable OTP read / write by setting PROGEN = 1 in the PROG register
// 13. Start the OTP burn procedure by setting PROGOTP = 1 in the PROG register
// 14. Read the PROG register until it reads 0x0001 (Programming procedure complete)
// 15. Clear the memory content by writing 0x00 in the whole non-volatile memory
// 16. Set the PROGVER = 1 to set the Guard band for the guard band test.1
// 17. Refresh the non-volatile memory content with the OTP content by setting OTPREF = 1
// 18. Read reg(0x0016) to reg(0x001B) → read register step2
// 19. Comparison of written content (settings and angle) with content of read register step2. 
//     If a deviation in the comparison occurs, the guard band test was not successful. 
//     Reprogramming is not allowed! Mandatory: guard band test
// 20. New power on cycle.
// 21. Read reg(0x0016) to Reg(0x001B) → read register step3
// 22. Comparison of written content (settings and angle) with content of read register step3. 
//     If a deviation in the comparison occurs, the power on test was not successful. 
//     Reprogramming is not allowed!
// 23. If point 18 is correct, the programming was successful.

#define CS_PIN 42

uint8_t crc8(unsigned char *data ,int length) {
    uint32_t crc = 0xC4;
    for (uint8_t i=0;i<length;i++) {
        crc ^= data[i];
        for (uint8_t bit=0;bit<8;bit++) {
            if ( (crc & 0x80)!=0 ) {
                crc <<= 1;
                crc ^= 0x1D;
            }
            else {
                crc <<= 1;
            }
        }
    }
    return (~crc)&0xFF;
}

uint32_t readRegister(uint16_t address) {
  uint8_t msg[3];
  msg[0] = ((address >> 8) & 0x3F) | 0x40; // Upper part of address and read flag
  msg[1] = (address & 0x00FF); // Lower part of address
  msg[2] = crc8(msg,2);
  // First 24bit transaction
  delayMicroseconds(10);
  digitalWrite(CS_PIN, LOW); // CS high
  SPI.transfer(msg[0]);
  SPI.transfer(msg[1]); 
  SPI.transfer(msg[2]); 
  digitalWrite(CS_PIN, HIGH); // CS high
  // Second 24bit transaction
  delayMicroseconds(10);
  digitalWrite(CS_PIN, LOW); // CS high
  union { uint32_t out; uint8_t in[4]; } answer;
  answer.in[3] = 0;
  answer.in[2] = SPI.transfer(msg[0]);
  answer.in[1] = SPI.transfer(msg[1]);
  answer.in[0] = SPI.transfer(msg[2]); 
  digitalWrite(CS_PIN, HIGH); // CS high
  return answer.out;
}

uint16_t readRegister16(uint16_t address) {
  uint8_t msg[3];
  msg[0] = ((address >> 8) & 0x3F) | 0x40; // Upper part of address and read flag
  msg[1] = (address & 0x00FF); // Lower part of address
  msg[2] = crc8(msg,2);
  // First 24bit transaction
  delayMicroseconds(10);
  digitalWrite(CS_PIN, LOW); // CS high
  SPI.transfer(msg[0]);
  SPI.transfer(msg[1]); 
  SPI.transfer(msg[2]); 
  digitalWrite(CS_PIN, HIGH); // CS high
  // Second 24bit transaction
  delayMicroseconds(10);
  digitalWrite(CS_PIN, LOW); // CS high
  union { uint16_t out; uint8_t in[2]; } answer;

  // EDIT: I switched the 0 in  answer.in[0] to a 1 and the same of the other
  answer.in[1] = SPI.transfer(msg[0]);
  answer.in[0] = SPI.transfer(msg[1]);
  SPI.transfer(msg[2]); 
  digitalWrite(CS_PIN, HIGH); // CS high
  return answer.out & 0x3F;
}

void writeRegister(uint16_t address, uint16_t data) {
  uint8_t msg[3];
  msg[0] = ((address >> 8) & 0x3F); // Upper part of address and write flag
  msg[1] = (address & 0x00FF); // Lower part of address
  msg[2] = crc8(msg,2);
  // First 16bit transaction
  delayMicroseconds(10);
  digitalWrite(CS_PIN, LOW); // CS high
  SPI.transfer(msg[0]);
  SPI.transfer(msg[1]); 
  SPI.transfer(msg[2]); 
  digitalWrite(CS_PIN, HIGH); // CS high
  // Second 16bit transaction
  msg[0] = ((data >> 8) & 0x00FF); // Upper part of address
  msg[1] = (data & 0x00FF); // Lower part of address
  msg[2] = crc8(msg,2);
  delayMicroseconds(10);
  digitalWrite(CS_PIN, LOW); // CS high
  SPI.transfer(msg[0]);
  SPI.transfer(msg[1]); 
  SPI.transfer(msg[2]); 
  digitalWrite(CS_PIN, HIGH); // CS high
}

void setup() {
  Serial.begin(115200);
  while (!Serial);

  // Configure SPI
  pinMode(CS_PIN, OUTPUT); // SS
  digitalWrite(8, HIGH); // CS high
  pinMode(7, OUTPUT); // MOSI
  // MISO D6
  pinMode(5, OUTPUT); // SCK
  SPI.begin();
  SPI.beginTransaction(SPISettings(1000000, MSBFIRST, SPI_MODE1));
}

void loop() {
  Serial.println("Reading error register");
  Serial.print("0x0001 "); Serial.println(readRegister(0x0001), HEX);
  
    // ==> OTP sequence
  Serial.println("Writing volatile register content");
  // Write registers content once
  // DISABLE 0x0015
  // FILTER_disable na ABI_off UVW_off 
  // 0              0  0       1
  writeRegister(0x0015,0x0001);
  // ZPOSM & ZPOSL
  uint16_t zeroPos = 0; // 14bit
  writeRegister(0x0016, (zeroPos >> 6) & 0x00FF );
  writeRegister(0x0017, (zeroPos << 2) & 0x00FC );
  // SETTINGS1, default 0x0000, leave as is
  writeRegister(0x0018, 0x0000 );
  // SETTINGS2
  // PWMon Data_select ABI_DEC DAECDIS UVW_ABI DIR NOISESET IWIDTH   
  // 0     0           0       0       0       0   1        1
  writeRegister(0x0019, 0b00000011 );
  // SETTINGS3
  // UVWPP HYS ABIRES
  // ABIRES HYS UVWPP
  // 000   00  000
  // 101   00  000
  writeRegister(0x001A, 0b10000000 );
  // Readback
  Serial.println("Reading volatile register content");
  Serial.print("0x0015 "); Serial.println(readRegister(0x0015), HEX);
  Serial.print("0x0016 "); Serial.println(readRegister(0x0016), HEX);
  Serial.print("0x0017 "); Serial.println(readRegister(0x0017), HEX);
  Serial.print("0x0018 "); Serial.println(readRegister(0x0018), HEX);
  Serial.print("0x0019 "); Serial.println(readRegister(0x0019), HEX);
  Serial.print("0x001A "); Serial.println(readRegister(0x001A), HEX);
  // ECC
  Serial.println("Generate ECC");
  writeRegister(0x001B, 0x0080 );
  uint16_t ecc = readRegister16(0x3FD0);
  Serial.print("0x3FD0 "); Serial.println(ecc, HEX);
  writeRegister(0x001B, ecc | 0x0080);
  readRegister(0x0001); // Read the error, which was caused by the checksum change
  // Readback
  Serial.println("Reading volatile register content + ecc");
  Serial.print("0x0015 "); Serial.println(readRegister(0x0015), HEX);
  Serial.print("0x0016 "); Serial.println(readRegister(0x0016), HEX);
  Serial.print("0x0017 "); Serial.println(readRegister(0x0017), HEX);
  Serial.print("0x0018 "); Serial.println(readRegister(0x0018), HEX);
  Serial.print("0x0019 "); Serial.println(readRegister(0x0019), BIN);
  Serial.print("0x001A "); Serial.println(readRegister(0x001A), BIN);
  Serial.print("0x001B "); Serial.println(readRegister(0x001B), HEX);
  // Danger
  // ===========================================================================================
  while(1);
  // ===========================================================================================  
  Serial.println("Writing OTP");
  // Unlock OTP area
  writeRegister(0x0003, 0x0001 );
  // Start OTP burning
  writeRegister(0x0003, 0x0008 );
  // Read OTP_CTRL
  uint16_t reg3 = 0;
  while (reg3 != 0x0001) {
    reg3 = readRegister16(0x0003);
  }
  // Clear memory
  writeRegister(0x0015, 0x0000);
  writeRegister(0x0016, 0x0000);
  writeRegister(0x0017, 0x0000);
  writeRegister(0x0018, 0x0000);
  writeRegister(0x0019, 0x0000);
  writeRegister(0x001A, 0x0000);
  writeRegister(0x001B, 0x0000);
  // Set Guardband
  writeRegister(0x0003, 0x0040);
  // Refresh memory with OTP content
  writeRegister(0x0003, 0x0004);
  // Readback
  Serial.println("Reading non-volatile register content");
  Serial.print("0x0015 "); Serial.println(readRegister(0x0015), HEX);
  Serial.print("0x0016 "); Serial.println(readRegister(0x0016), HEX);
  Serial.print("0x0017 "); Serial.println(readRegister(0x0017), HEX);
  Serial.print("0x0018 "); Serial.println(readRegister(0x0018), HEX);
  Serial.print("0x0019 "); Serial.println(readRegister(0x0019), HEX);
  Serial.print("0x001A "); Serial.println(readRegister(0x001A), HEX);
  Serial.print("0x001B "); Serial.println(readRegister(0x001B), HEX);
  Serial.println("If those registers do not fit the chip is bricked...");
  while(1);
}

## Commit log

2020-11-11 adding Inital Files
    [AI3M_print2_file.3mf, Martin_print2_side-fesupport_fecover.3mf, Martin_print3_3coveraa-1coverfe-1baseupperleg.3mf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]
2020-11-11 images of new covers
    [cover_hip_aa.stl, cover_hip_fe.stl, cover_upper_leg.stl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]
2020-11-11 electrical changes
    [PCB_2020-10-29_13-03-39_2020-11-11_17-29-31.pcbdoc, cover_hip_aa.stl, cover_hip_fe.stl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]
2020-11-11 added encoder photo
2020-11-11 links for Pulley
2020-11-11 pulley cahnges
2020-11-27 Foot Contact Switch
    [Sheet_1_2020-11-27_13-26-31.schdoc, body_structure_back.STL, body_structure_bottom.STL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]
2020-11-27 Foot contact Sensor
2020-11-27 images and gerber of foot switch added
2020-11-27 arduino config added
2020-11-27 added images for pulleys. Pdf links work
2020-12-19 Images for encoders
    [Ankle.stl, Body_new_IMU.stl, main Body.stl]
2021-03-04 Adding more images
    [Foot_new_2.stl, ankle_new_2.stl, ankle_new_3.stl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]
2021-03-04 Adding Arduino code
2021-03-10 Initial Commit
    Moved all data te new Repository
    [Sheet_1_2020-11-27_13-26-31.schdoc]
